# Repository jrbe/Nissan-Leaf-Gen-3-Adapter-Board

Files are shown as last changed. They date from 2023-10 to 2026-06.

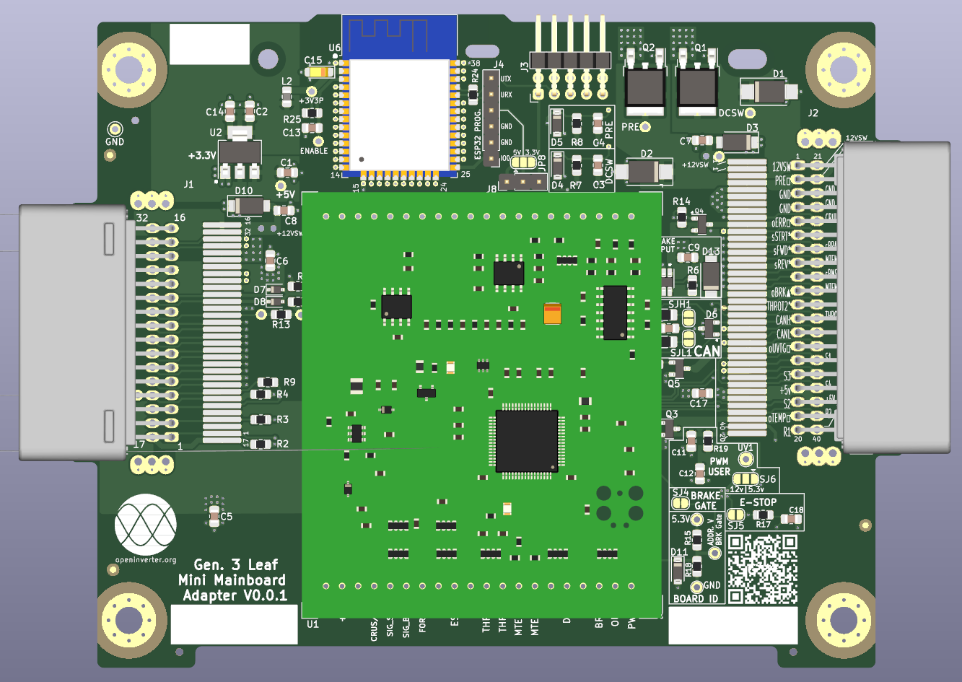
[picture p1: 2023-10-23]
Front PCB Assembly.PNG

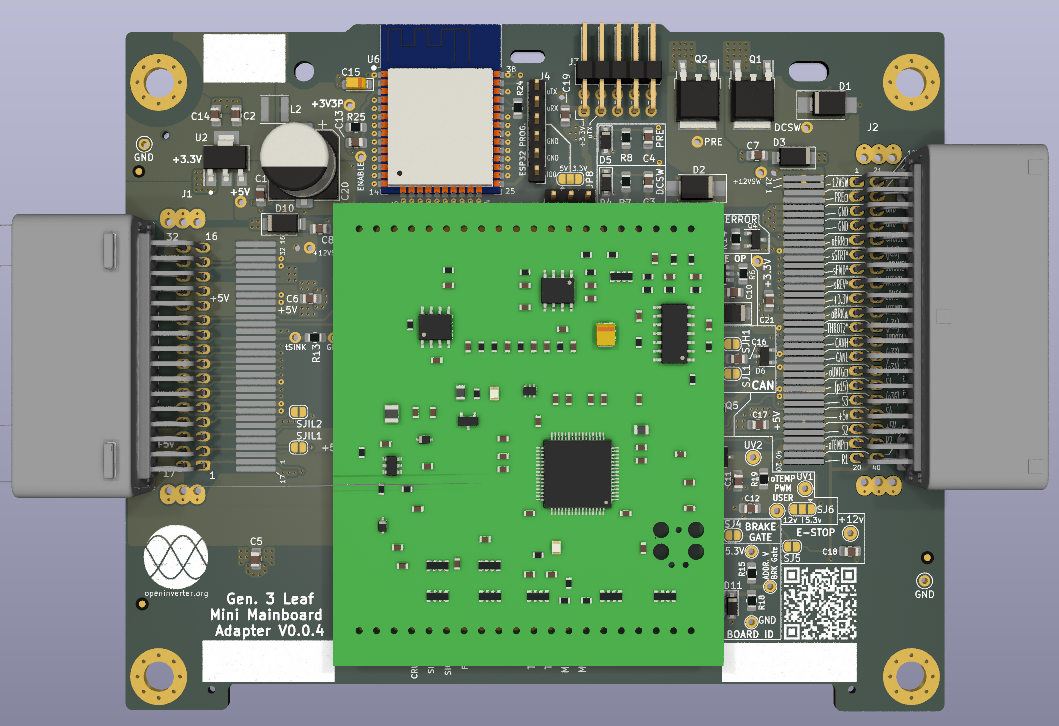
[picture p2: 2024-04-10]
V0.0.4/PC Board Images/All.PNG

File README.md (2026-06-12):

# Nissan-Leaf-Gen-3-Adapter-Board
This is an Open Inverter Mini Mainboard adapter PC board for a Gen. 3 Nissan Leaf inverter. This gives a user full control over the inverter for DIY EV projects. Designed in Kicad 7.

This is a work in progress, V0.0.4 is current but is not a production release yet.  Johu (Open Inverter) could not get a motor spinning in closed loop control. There are also many board settings to work out still.

The Wiki for this board is here, https://openinverter.org/wiki/Nissan_Leaf_Gen_3_(2018_up_EM57)

There are many options built into this board. Multi-footprints for the 2 main connectors for SMD and through hole options, E-stop bypass or use, auxiliary outputs with different voltages, etc. See the wiki above for details.

If you have questions please check the Wiki first.  If your question is not answered there please post questions, comments, ideas, etc. in this thread, [https://openinverter.org/forum/viewtopic.php?t=4565](https://openinverter.org/forum/viewtopic.php?t=4565)

Front PCB w- SMD

PCB back

The original development thread is here, https://openinverter.org/forum/viewtopic.php?t=2324  Please do not post questions here.

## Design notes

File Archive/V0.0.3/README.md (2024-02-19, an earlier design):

# Nissan-Leaf-Gen-3-Adapter-Board
Open Inverter Mini Mainboard adapter PC board for a Gen. 3 Nissan Leaf inverter. Designed in Kicad 6.

**Currently working on V0.0.4, I'd suggest waiting for this new version as a few errors will prevent this from working properly.**

This is a work in progress to control the Gen 3 Nissan Leaf inverter with an Open Inverter Mini Mainboard.  There are a few unknowns still at the time of writing this that are all covered in the Wiki.

The Wiki for this board is here, https://openinverter.org/wiki/Nissan_Leaf_Gen_3_(2018_up_EM57)

The original development thread is here, https://openinverter.org/forum/viewtopic.php?t=2324  Please do not post questions here.

If you have questions please check the Wiki first.  If your question is not answered there please post questions, comments, ideas, etc. in this thread, https://openinverter.org/forum/viewtopic.php?t=4276

Front PCB Assembly

Front PCB w- SMD

PCB back

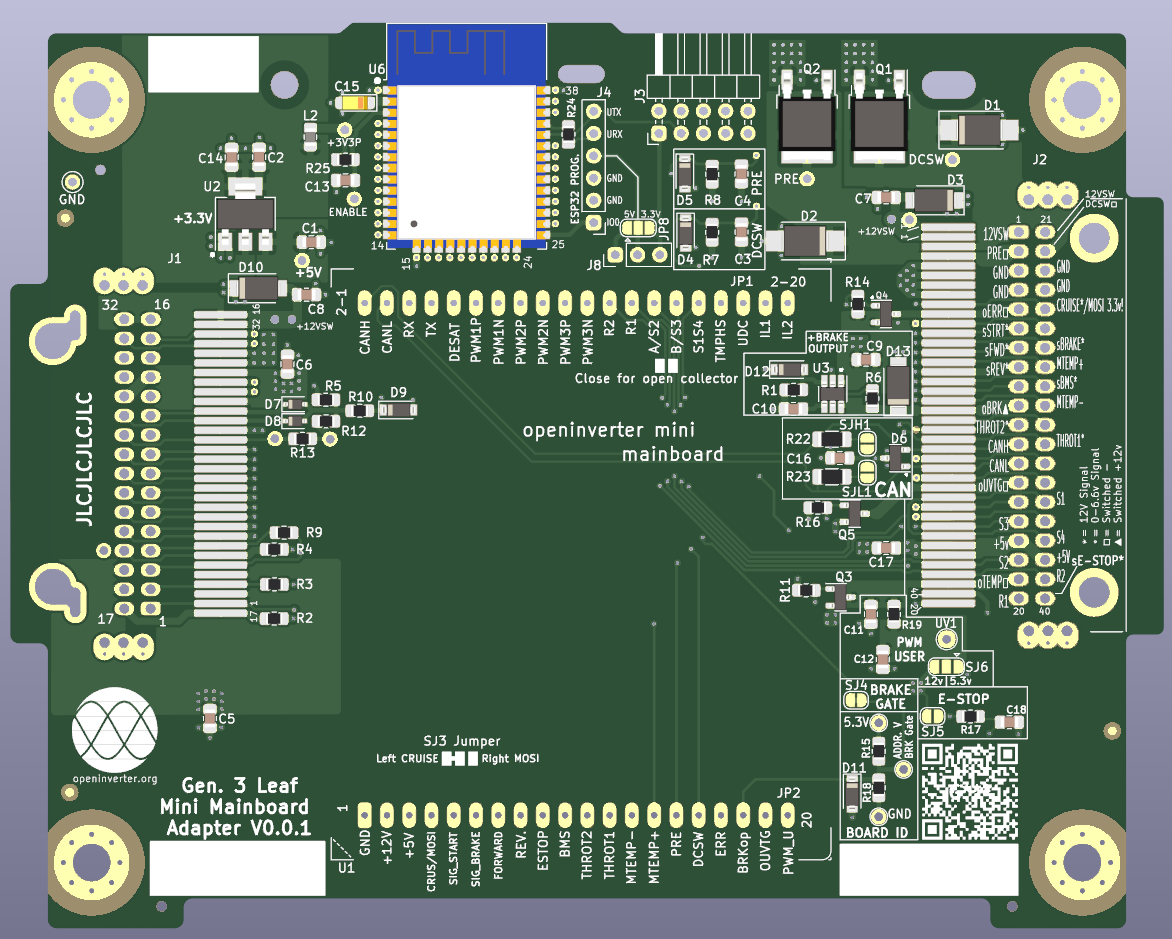
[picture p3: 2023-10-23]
Front PCB w- SMD.PNG

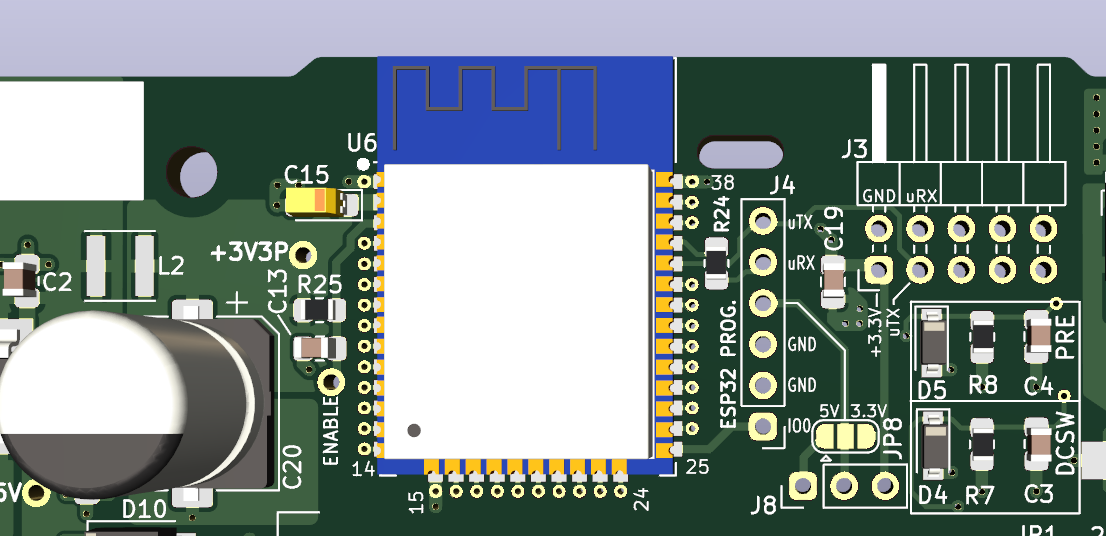
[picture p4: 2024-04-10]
V0.0.4/PC Board Images/ESP32.PNG

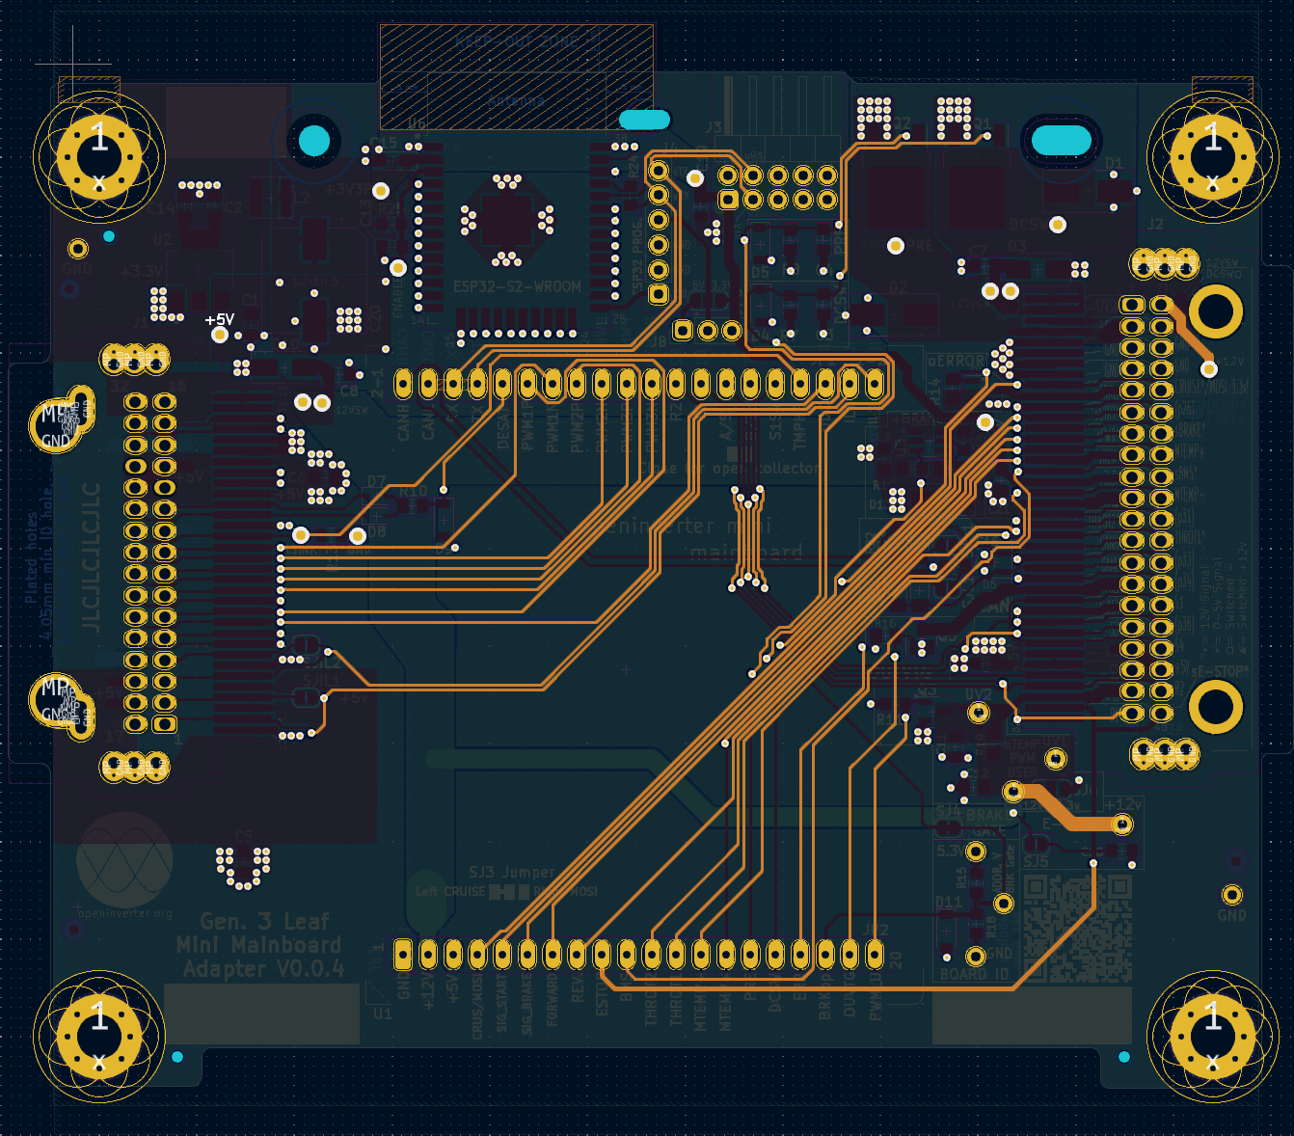
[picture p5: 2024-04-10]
V0.0.4/PC Board Images/3rd Layer, In3Sig.PNG

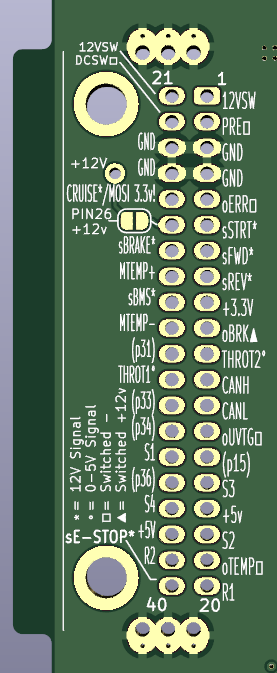
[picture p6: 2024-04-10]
V0.0.4/PC Board Images/40 pos. conn back.PNG

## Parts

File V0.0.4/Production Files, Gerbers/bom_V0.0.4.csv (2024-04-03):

Designator | Footprint | Quantity | Value | LCSC Part #
5.3V1, TP12, TP_A1, TP_GND1_2, TP_GND1, TP_GND2, UV1, UV2, UV3 | TestPoint_THTPad_D2.0mm_Drill1.0mm | 9 | TestPoint | -
C1, C12, C14, C18, C2, C9 | 0805 | 6 | 1uF | C28323
C11, C13, C7, C8 | 0805 | 4 | 100nF | C28233
C15 | CP_EIA-3216-18_Kemet-A_Pad1.58x1.35mm_HandSolder | 1 | 10uF T | C7171
C16 | 0805 | 1 | 4.7nF | C1744
C17, C21, C5, C6 | 0805 | 4 | 10uF | C15850
D1, D2 | D_SMB_Handsoldering | 2 | D_Zener | C1972924
D10, D13, D3 | D_SMA | 3 | SMAJ15CA-TP | C129543
D11, D4, D5, D9 | D_SOD-123 | 4 | MM1Z3B3 | C108453
D6 | SOT-23 | 1 | SP0502BAHT | C907838
D7, D8 | D_SOD-323 | 2 | 1N5819WS Schottky | C191023
H1, H2, H3, H4 | MountingHole_4.3mm_M4_Pad_Via | 4 | MountingHole_Pad | -
H5, H6 | MountingHole_4.3mm_M4 | 2 | MountingHole | -
J4 | PinHeader_1x06_P2.54mm_Vertical | 1 | Conn_01x06_Male | DNP
J8 | PinHeader_1x03_P2.54mm_Vertical | 1 | Conn_01x03_Male | DNP
JP8, SJ6 | SolderJumper-3_P1.3mm_Open_RoundedPad1.0x1.5mm | 2 | Jumper_3_Open | -
L2 | Inductor_Sunlord_4030 | 1 | 10uH | C38117
Q1, Q2 | TO-252-2 | 2 | Q_NMOS_GDS | C3017
Q3, Q4, Q5 | SOT-23 | 3 | IRLML0100TRPBF | C53658
R10 | 0805 | 1 | 470R | C17710
R11, R14, R16, R7, R8 | 0805 | 5 | 10K | C17414
R13 | 0805 | 1 | 1k2 | C17379
R15 | 0805 | 1 | 47K 1pct. | C17713
R18, R25 | 0805 | 2 | 4K7 1pct. | C17673
R22, R23, R32, R33 | 1206 | 4 | 120R .5pct 0.125W+ | C2984524
R24 | 0805 | 1 | 499R | C17722
SJ4 | SolderJumper-2_P1.3mm_Bridged_RoundedPad1.0x1.5mm | 1 | SolderJumper_2_Bridged | -
SJ5 | SolderJumper-2_P1.3mm_Open_RoundedPad1.0x1.5mm | 1 | SolderJumper_2_Bridged | -
SJ9, SJH1, SJIL1, SJIL2, SJL1 | SolderJumper-2_P1.3mm_Open_RoundedPad1.0x1.5mm | 5 | SolderJumper_2_Open | -
U1 | OPENINVERTER_MINI_MAINBOARD | 1 | OpenInverter_Mini_Mainboard-openinverter_mini_mainboard | -
U2 | SOT-223-3_TabPin2 | 1 | AP1117-33 | C6186
U3 | SOT-23-6_Handsoldering | 1 | TPS22810DBVR | C205990
U6 | ESP32-WROOM-32 | 1 | ESP32-S2-WROOM | C82899

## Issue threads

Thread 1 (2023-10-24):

E-Stop / R17 value too high

jrbe, 2023-10-24:
R17 needs to be a very low value to work with the 4k7 / 1k2 voltage divider on the mini mainboard.  As it is in V0.0.1 the e-stop signal will never be seen as high.

jrbe, 2023-10-24:
Removed R17.  Upreved to V0.0.2.

Closed 2023-10-24.

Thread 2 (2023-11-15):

L2 inductor too small

jrbe, 2023-11-15:
The L2 inductor is only rated for 15ma.

jrbe, 2023-11-15:
Changed to a Sunlord 4030 AKA 4x4mm inductor footprint & upreved to V0.0.3.

Closed 2023-11-15.

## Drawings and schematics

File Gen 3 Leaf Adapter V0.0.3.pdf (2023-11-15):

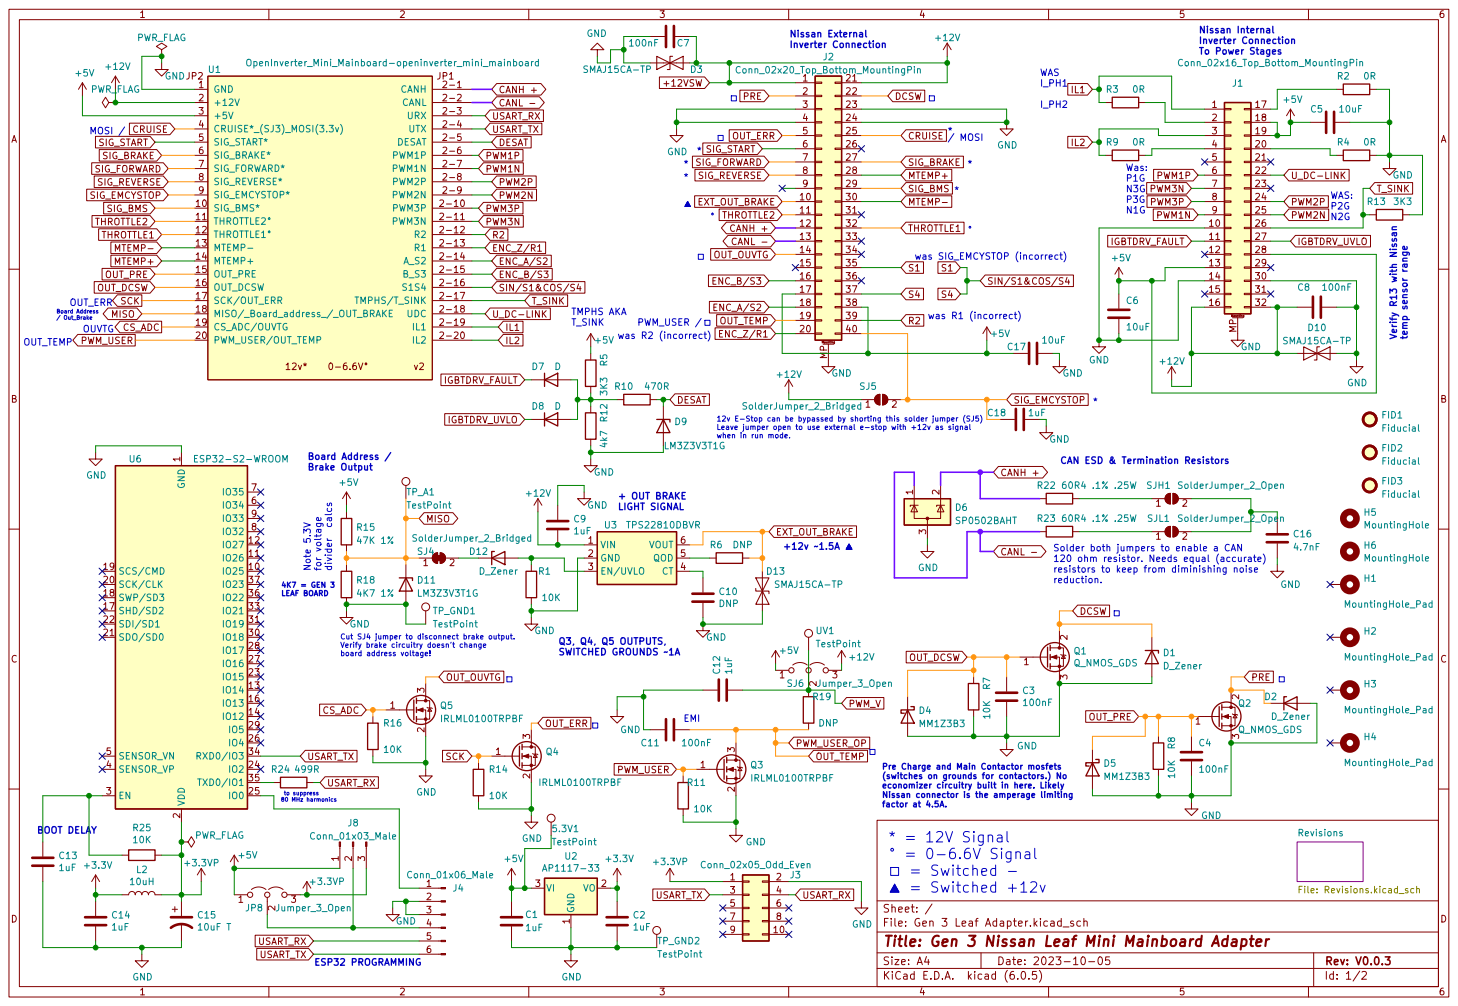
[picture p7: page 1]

To Power Stages + OUT BRAKE
I_PH2 Solder both jumpers to enable a CAN

SCK
PWM_V MISO
resistors to keep from diminishing noise reduction. OUVTG
PWM_USER

120 ohm resistor. Needs equal (accurate)

2 SCK/CLK 20 SDO/SD0 21 SDI/SD1 22

factor at 4.5A. þÿ%¡
Pre Charge and Main Contactor mosfets
(switches on grounds for contactors.) No
economizer circuitry built in here. Likely Nissan connector is the amperage limiting

Id: 1/2 Title: Gen 3 Nissan Leaf Mini Mainboard Adapter

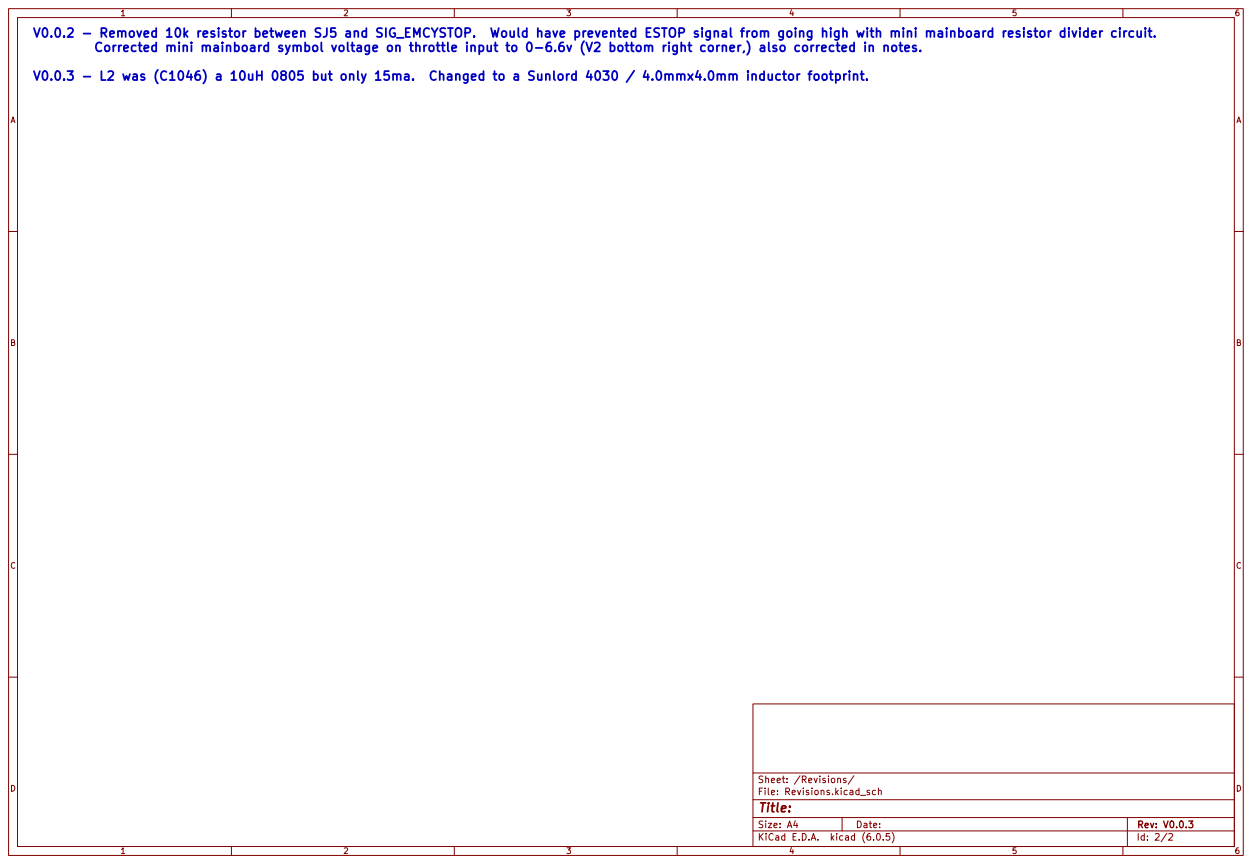
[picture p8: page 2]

V0.0.2 - Removed 10k resistor between SJ5 and SIG_EMCYSTOP. Would have prevented ESTOP signal from going high with mini mainboard resistor divider circuit.
Corrected mini mainboard symbol voltage on throttle input to 0-6.6v (V2 bottom right corner,) also corrected in notes.

V0.0.3 - L2 was (C1046) a 10uH 0805 but only 15ma. Changed to a Sunlord 4030 / 4.0mmx4.0mm inductor footprint.

File: Revisions.kicad_sch Sheet: /Revisions/
Id: 2/2 Title:

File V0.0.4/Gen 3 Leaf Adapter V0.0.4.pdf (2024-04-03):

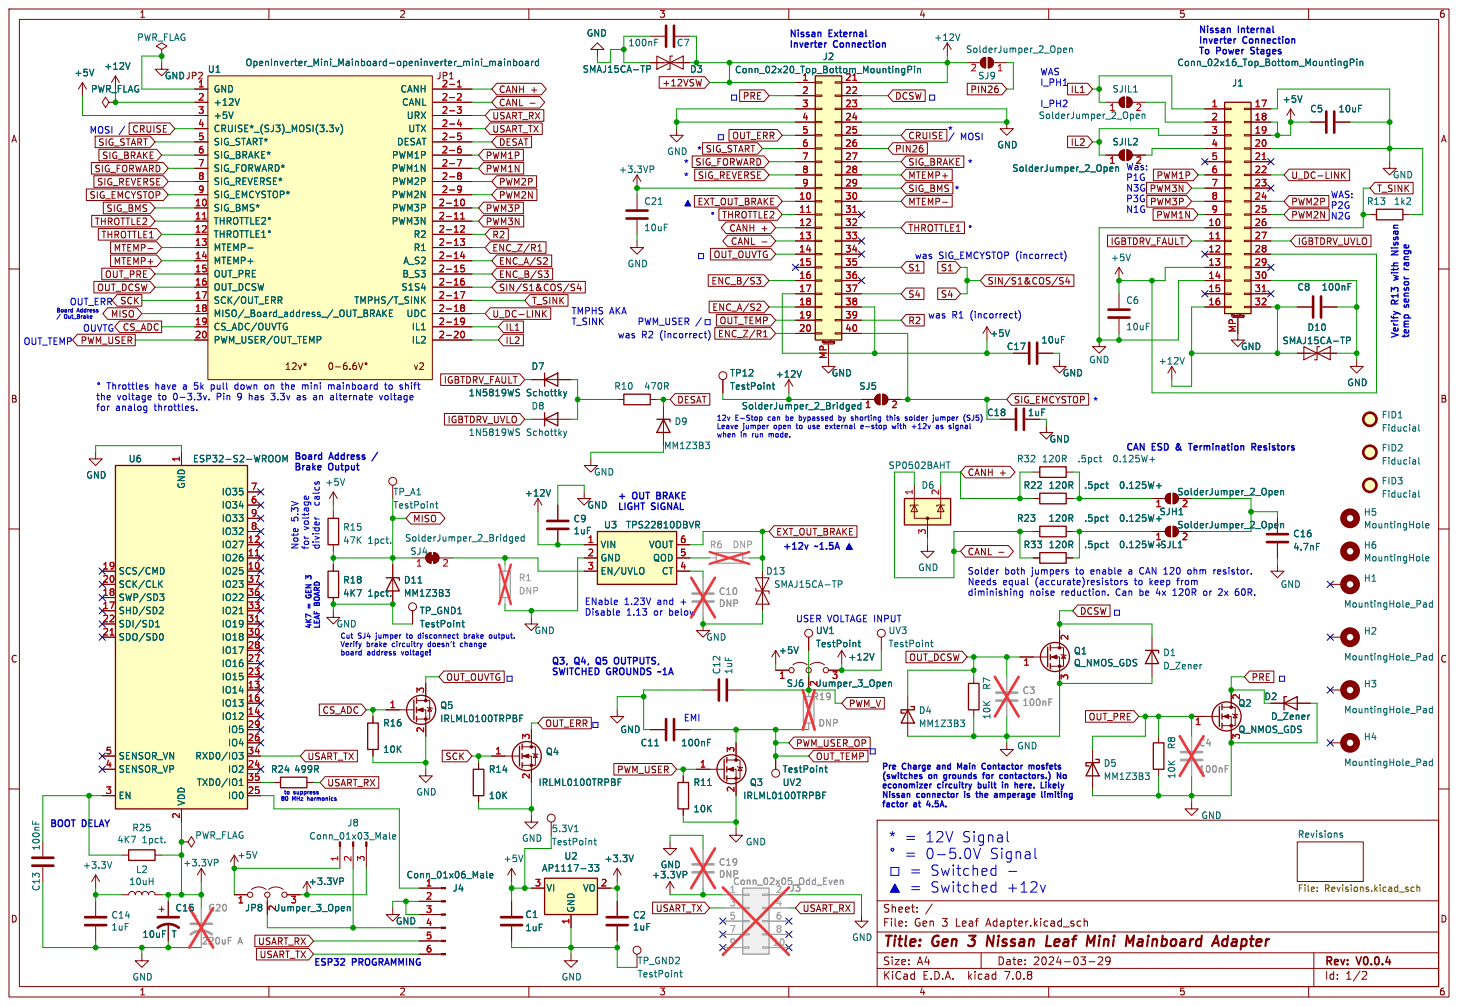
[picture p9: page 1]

GND
To Power Stages Q3, Q4, Q5 OUTPUTS, SWITCHED GROUNDS ~1A

2 SCK/CLK 20 SDO/SD0 21 SDI/SD1 22

Pre Charge and Main Contactor mosfets
factor at 4.5A.
* = 12V Signal
þÿ%¡ = Switched - þÿ%² = Switched +12v

to suppress 80 MHz harmonics

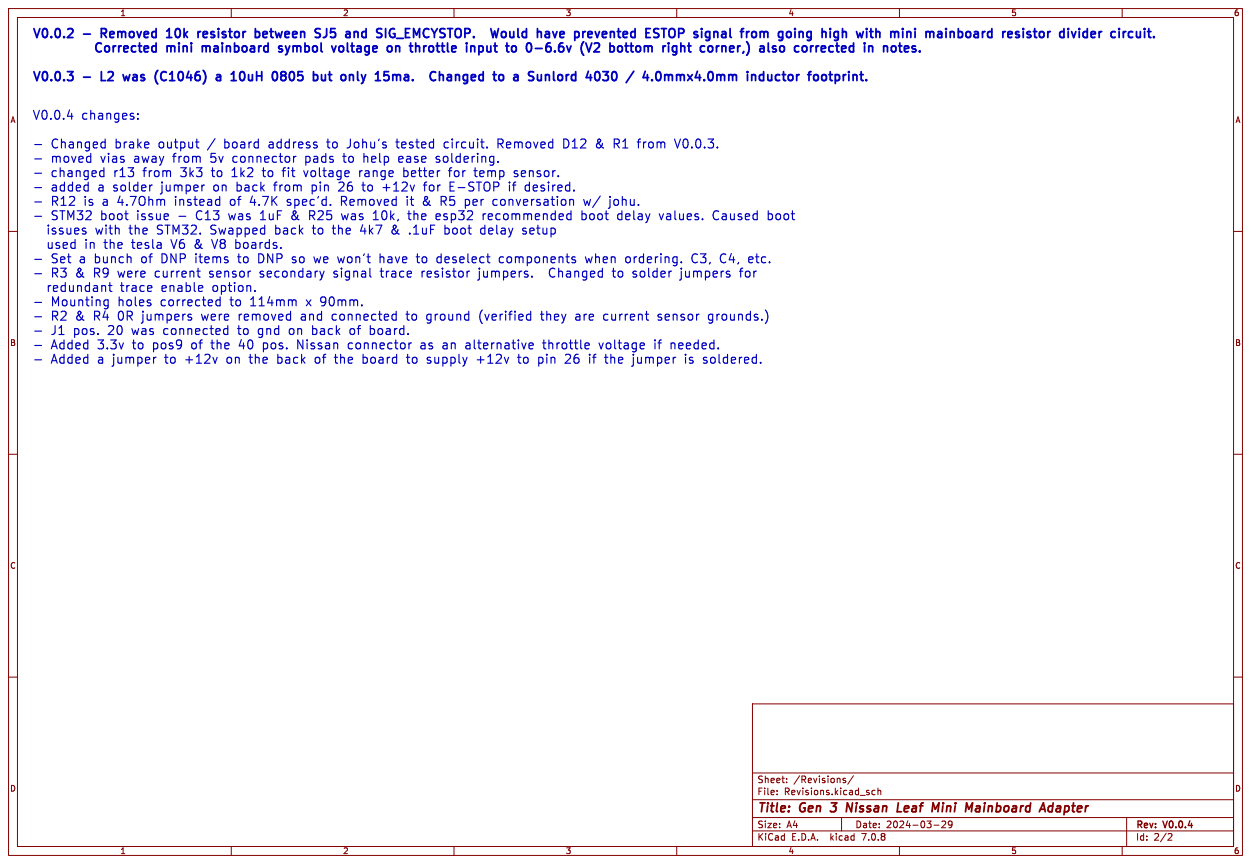
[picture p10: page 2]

issues with the STM32. Swapped back to the 4k7 & .1uF boot delay setup

redundant trace enable option. - Mounting holes corrected to 114mm x 90mm. - R2 & R4 0R jumpers were removed and connected to ground (verified they are current sensor grounds.)

- J1 pos. 20 was connected to gnd on back of board. - Added 3.3v to pos9 of the 40 pos. Nissan connector as an alternative throttle voltage if needed. - Added a jumper to +12v on the back of the board to supply +12v to pin 26 if the jumper is soldered.

Id: 2/2 Title: Gen 3 Nissan Leaf Mini Mainboard Adapter File: Revisions.kicad_sch Sheet: /Revisions/

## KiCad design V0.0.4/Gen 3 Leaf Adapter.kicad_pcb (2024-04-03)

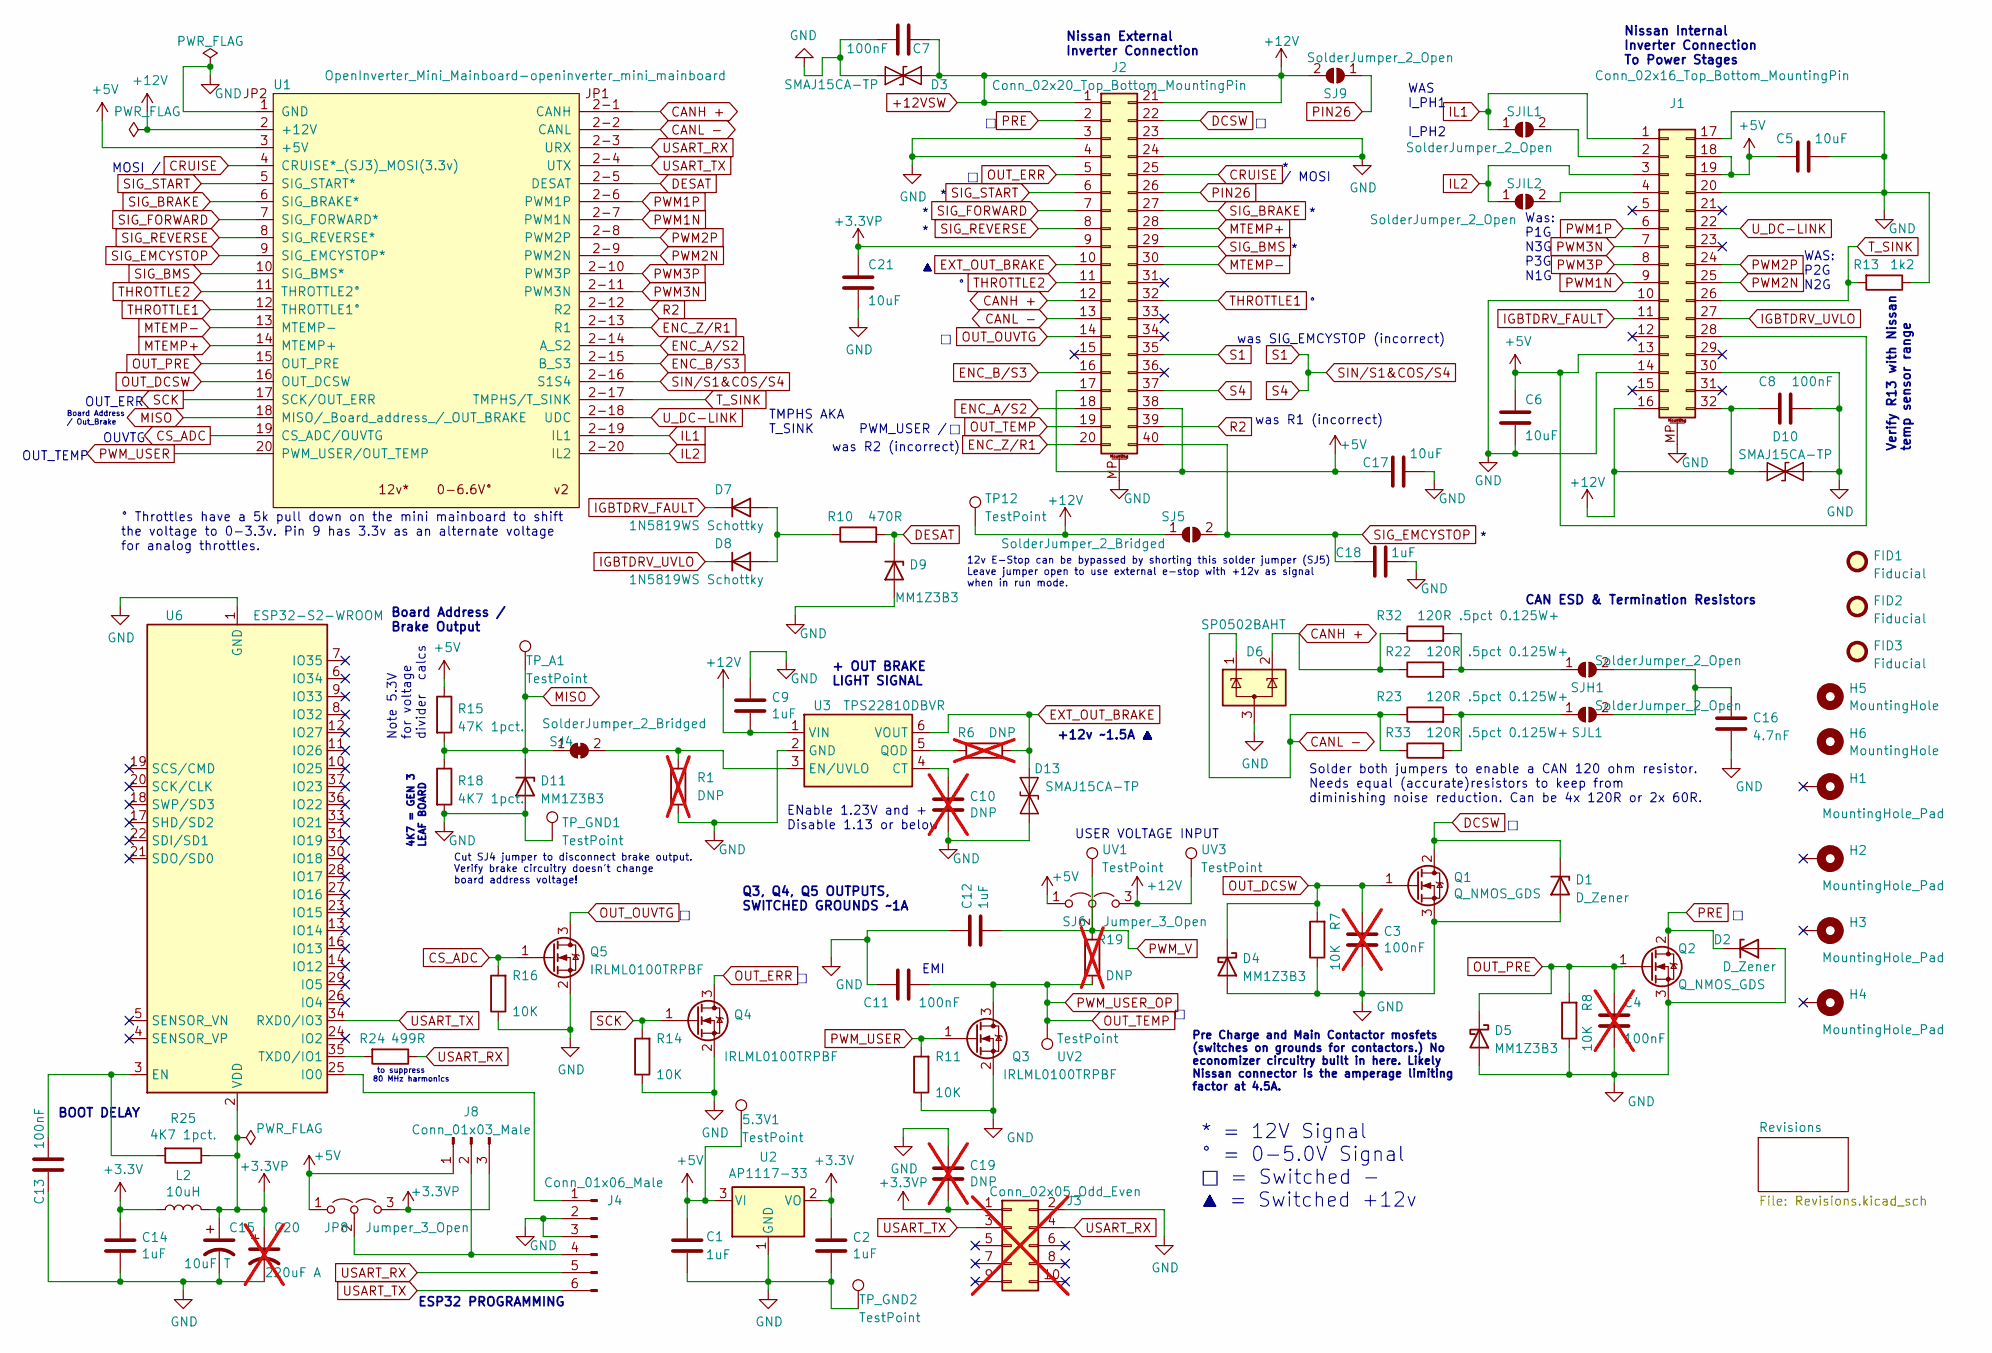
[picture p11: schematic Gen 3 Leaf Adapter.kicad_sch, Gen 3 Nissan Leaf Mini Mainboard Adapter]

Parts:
5.3V1: TestPoint; TestPoint_THTPad_D2.0mm_Drill1.0mm
C1, C2, C9, C12, C14, C18: 1uF; C_0805_2012Metric_Pad1.18x1.45mm_HandSolder; MFG Part # CL21B105KBFNNNE; LCSC Part C28323
C3, C4: 100nF; C_0805_2012Metric_Pad1.18x1.45mm_HandSolder; MFG Part # CL21B104KCFNNNE; LCSC Part C28233; not fitted
C5, C6, C17, C21: 10uF; C_0805_2012Metric_Pad1.18x1.45mm_HandSolder; MFG Part # CL21A106KAYNNNE; LCSC Part C15850
C7, C8, C11, C13: 100nF; C_0805_2012Metric_Pad1.18x1.45mm_HandSolder; MFG Part # CL21B104KCFNNNE; LCSC Part C28233
C10: DNP; C_0805_2012Metric_Pad1.18x1.45mm_HandSolder; LCSC Part DNP; not fitted
C15: 10uF T; CP_EIA-3216-18_Kemet-A_Pad1.58x1.35mm_HandSolder; MFG Part # TAJA106K016RNJ; LCSC Part C7171
C16: 4.7nF; C_0805_2012Metric_Pad1.18x1.45mm_HandSolder; MFG Part # 0805B472K500NT; LCSC Part C1744
C19: DNP; C_0805_2012Metric_Pad1.18x1.45mm_HandSolder; not fitted
C20: 220uF A; CP_Elec_10x10.5; not fitted
D1, D2: D_Zener; D_SMB_Handsoldering; LCSC Part C1972924
D3, D10, D13: SMAJ15CA-TP; D_SMA; MFG Part # SMAJ15CA-TP; LCSC Part C129543
D4, D5, D9, D11: MM1Z3B3; D_SOD-123; MFG Part # MM1Z3B3; LCSC Part C108453
D6: SP0502BAHT; SOT-23; MFG Part # PESD1CAN; LCSC Part C907838
D7, D8: 1N5819WS Schottky; D_SOD-323; MFG Part # 1N5819WS; LCSC Part C191023
FID1, FID2, FID3: Fiducial; Fiducial_1mm_Mask2mm
H1, H2, H3, H4: MountingHole_Pad; MountingHole_4.3mm_M4_Pad_Via
H5, H6: MountingHole; MountingHole_4.3mm_M4
J1: Conn_02x16_Top_Bottom_MountingPin; 32 Pin Internal Nissan Inverter Connector Merged Footprints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; LCSC Part DNP
J2: Conn_02x20_Top_Bottom_MountingPin; TE_1318384-2_Dual_FP; LCSC Part DNP
J3: Conn_02x05_Odd_Even; PinHeader_2x05_P2.54mm_Horizontal; LCSC Part DNP; not fitted
J4: Conn_01x06_Male; PinHeader_1x06_P2.54mm_Vertical; LCSC Part DNP
J8: Conn_01x03_Male; PinHeader_1x03_P2.54mm_Vertical; LCSC Part DNP
JP8: Jumper_3_Open; SolderJumper-3_P1.3mm_Open_RoundedPad1.0x1.5mm
L2: 10uH; Inductor_Sunlord_4030; MFG Part # SWPA4030S100MT; LCSC Part C38117
Q1, Q2: Q_NMOS_GDS; TO-252-2; MFG Part # IRLR3410TRPBF; LCSC Part C3017
Q3, Q4, Q5: IRLML0100TRPBF; SOT-23; MFG Part # IRLML0100TRPBF; LCSC Part C53658
R1: DNP; R_0805_2012Metric_Pad1.20x1.40mm_HandSolder; not fitted
R6, R19: DNP; R_0805_2012Metric_Pad1.20x1.40mm_HandSolder; LCSC Part DNP; not fitted
R7, R8, R11, R14, R16: 10K; R_0805_2012Metric_Pad1.20x1.40mm_HandSolder; MFG Part # 0805W8F1002T5E; LCSC Part C17414
R10: 470R; R_0805_2012Metric_Pad1.20x1.40mm_HandSolder; MFG Part # 0805W8F4700T5E; LCSC Part C17710
R13: 1k2; R_0805_2012Metric_Pad1.20x1.40mm_HandSolder; MFG Part # 0805W8F1201T5E; LCSC Part C17379
R15: 47K 1pct.; R_0805_2012Metric_Pad1.20x1.40mm_HandSolder; MFG Part # 0805W8F4702T5E; LCSC Part C17713
R18, R25: 4K7 1pct.; R_0805_2012Metric_Pad1.20x1.40mm_HandSolder; MFG Part # 0805W8F4701T5E; LCSC Part C17673
R22, R23, R32, R33: 120R .5pct 0.125W+; R_1206_3216Metric_Pad1.30x1.75mm_HandSolder; LCSC Part C2984524
R24: 499R; R_0805_2012Metric_Pad1.20x1.40mm_HandSolder; MFG Part # 0805W8F4990T5E; LCSC Part C17722
SJ4: SolderJumper_2_Bridged; SolderJumper-2_P1.3mm_Bridged_RoundedPad1.0x1.5mm
SJ5: SolderJumper_2_Bridged; SolderJumper-2_P1.3mm_Open_RoundedPad1.0x1.5mm
SJ6: Jumper_3_Open; SolderJumper-3_P1.3mm_Open_RoundedPad1.0x1.5mm
SJ9: SolderJumper_2_Open; SolderJumper-2_P1.3mm_Open_RoundedPad1.0x1.5mm
SJH1: SolderJumper_2_Open; SolderJumper-2_P1.3mm_Open_RoundedPad1.0x1.5mm
SJIL1, SJIL2: SolderJumper_2_Open; SolderJumper-2_P1.3mm_Open_RoundedPad1.0x1.5mm
SJL1: SolderJumper_2_Open; SolderJumper-2_P1.3mm_Open_RoundedPad1.0x1.5mm
TP12: TestPoint; TestPoint_THTPad_D2.0mm_Drill1.0mm
TP_A1: TestPoint; TestPoint_THTPad_D2.0mm_Drill1.0mm
TP_GND1, TP_GND2: TestPoint; TestPoint_THTPad_D2.0mm_Drill1.0mm
U1: OpenInverter_Mini_Mainboard-openinverter_mini_mai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; OPENINVERTER_MINI_MAINBOARD
U2: AP1117-33; SOT-223-3_TabPin2; MFG Part # AMS1117-3.3; LCSC Part C6186
U3: TPS22810DBVR; SOT-23-6_Handsoldering; MFG Part # TPS22810DBVR; LCSC Part C205990
U6: ESP32-S2-WROOM; ESP32-WROOM-32; MFG Part # ESP32-WROOM-32-N4; LCSC Part C82899
UV1, UV2, UV3: TestPoint; TestPoint_THTPad_D2.0mm_Drill1.0mm

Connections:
+3.3VP: C15.1, C19.2, C20.1, C21.1, J2.9, J3.1, J8.3, JP8.3 (B), L2.2, R25.1, U6.2 (VDD)
+3V3: C2.1, C14.1, L2.1, U2.2 (VO)
+5V: 5.3V1.1, C1.1, C5.1, C6.1, C17.1, J1.13, J1.18, J1.19, J1.28, J2.17, J2.38, J8.1, JP8.1 (A), R15.1, SJ6.1 (A), U1.3 (+5V), U2.3 (VI)
+12VSW: C7.1, C8.1, C9.2, D3.2 (A2), D10.2 (A2), J1.16, J1.32, J2.1, J2.21, SJ5.1 (A), SJ6.3 (B), SJ9.2 (B), TP12.1, U1.2 (+12V), U3.1 (VIN), UV3.1
CANH +: D6.2 (K), J2.12, R22.1, R32.1, U1.2-1 (CANH)
CANL -: D6.1 (K), J2.13, R23.1, R33.1, U1.2-2 (CANL)
CRUISE: J2.25, U1.4 (CRUISE*_(SJ3)_MOSI(3.3v))
CS_ADC: Q5.1 (G), R16.2, U1.19 (CS_ADC/OUVTG)
DCSW: D1.1 (K), J2.22, Q1.2 (D)
DESAT: D9.1 (K), R10.2, U1.2-5 (DESAT)
ENC_A/S2: J2.18, U1.2-14 (A_S2)
ENC_B/S3: J2.16, U1.2-15 (B_S3)
ENC_Z/R1: J2.20, U1.2-13 (R1)
EXT_OUT_BRAKE: D13.1 (A1), J2.10, R6.1, U3.6 (VOUT)
GND: C1.2, C2.2, C3.2, C4.2, C5.2, C6.2, C7.2, C8.2, C9.1, C10.2, C11.2, C12.1, C13.1, C14.2, C15.2, C16.2, C17.2, C18.2, C19.1, C20.2, C21.2, D1.2 (A), D2.2 (A), D3.1 (A1), D4.2 (A), D5.2 (A), D6.3 (A), D9.2 (A), D10.1 (A1), D11.2 (A), D13.2 (A2), J1.10, J1.14, J1.17, J1.20, J1.30, J1.MP (MountPin), J2.3, J2.4, J2.23, J2.24, J2.MP (MountPin), J3.2, J4.2, J4.3, Q1.3 (S), Q2.3 (S), Q3.2 (S), Q4.2 (S), Q5.2 (S), R1.2, R7.1, R8.1, R11.1, R13.1, R14.1, R16.1, R18.2, TP_GND1.1, TP_GND2.1, U1.1 (GND), U2.1 (GND), U3.2 (GND), U6.1 (GND), U6.15 (GND), U6.38 (GND), U6.39 (GND); also elsewhere on the board
IGBTDRV_FAULT: D7.1 (K), J1.11
IGBTDRV_UVLO: D8.1 (K), J1.27
IL1: J1.1, SJIL1.1 (A), U1.2-19 (IL1)
IL2: J1.3, SJIL2.1 (A), U1.2-20 (IL2)
MISO: D11.1 (K), R15.2, R18.1, SJ4.1 (A), TP_A1.1, U1.18 (MISO/_Board_address_/_OUT_BRAKE)
MTEMP+: J2.28, U1.14 (MTEMP+)
MTEMP-: J2.30, U1.13 (MTEMP-)
unnamed: D7.2 (A), D8.2 (A), R10.1
unnamed: J1.2, SJIL1.2 (B)
unnamed: J1.4, SJIL2.2 (B)
unnamed: J4.1, U6.25 (IO0)
unnamed: J4.4, J8.2, JP8.2 (C)
unnamed: R1.1, SJ4.2 (B), U3.3 (EN/UVLO)
unnamed: R22.2, R32.2, SJH1.1 (A)
unnamed: C16.1, SJH1.2 (B), SJL1.2 (B)
unnamed: R23.2, R33.2, SJL1.1 (A)
unnamed: C10.1, U3.4 (CT)
unnamed: R6.2, U3.5 (QOD)
unnamed: C13.2, R25.2, U6.3 (EN)
unnamed: R24.2, U6.35 (TXD0/IO1)
OUT_DCSW: C3.1, D4.1 (K), Q1.1 (G), R7.2, U1.16 (OUT_DCSW)
OUT_ERR: J2.5, Q4.3 (D)
OUT_OUVTG: J2.14, Q5.3 (D)
OUT_PRE: C4.1, D5.1 (K), Q2.1 (G), R8.2, U1.15 (OUT_PRE)
OUT_TEMP: C11.1, J2.19, Q3.3 (D), R19.1, UV2.1
PIN26: J2.26, SJ9.1 (A)
PRE: D2.1 (K), J2.2, Q2.2 (D)
PWM1N: J1.9, U1.2-7 (PWM1N)
PWM1P: J1.6, U1.2-6 (PWM1P)
PWM2N: J1.25, U1.2-9 (PWM2N)
PWM2P: J1.24, U1.2-8 (PWM2P)
PWM3N: J1.7, U1.2-11 (PWM3N)
PWM3P: J1.8, U1.2-10 (PWM3P)
PWM_USER: Q3.1 (G), R11.2, U1.20 (PWM_USER/OUT_TEMP)
PWM_V: C12.2, R19.2, SJ6.2 (C), UV1.1
R2: J2.39, U1.2-12 (R2)
S1: J2.35, J2.37, U1.2-16 (S1S4)
SCK: Q4.1 (G), R14.2, U1.17 (SCK/OUT_ERR)
SIG_BMS: J2.29, U1.10 (SIG_BMS*)
SIG_BRAKE: J2.27, U1.6 (SIG_BRAKE*)
SIG_EMCYSTOP: C18.1, J2.40, SJ5.2 (B), U1.9 (SIG_EMCYSTOP*)
SIG_FORWARD: J2.7, U1.7 (SIG_FORWARD*)
SIG_REVERSE: J2.8, U1.8 (SIG_REVERSE*)
SIG_START: J2.6, U1.5 (SIG_START*)
THROTTLE1: J2.32, U1.12 (THROTTLE1°)
THROTTLE2: J2.11, U1.11 (THROTTLE2°)
T_SINK: J1.26, R13.2, U1.2-17 (TMPHS/T_SINK)
USART_RX: J3.4, J4.5, R24.1, U1.2-3 (URX)
USART_TX: J3.3, J4.6, U1.2-4 (UTX), U6.34 (RXD0/IO3)
U_DC-LINK: J1.22, U1.2-18 (UDC)

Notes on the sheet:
PWM_USER /
4K7 = GEN 3 LEAF BOARD
OUT_ERR
/ MOSI
+ OUT BRAKE LIGHT SIGNAL
Was: P1G N3G P3G N1G
BOOT DELAY
TMPHS AKA T_SINK
MOSI /
* = 12V Signal ° = 0-5.0V Signal □ = Switched - ▲ = Switched +12v
EMI
Solder both jumpers to enable a CAN 120 ohm resistor. Needs equal (accurate)resistors to keep from diminishing noise reduction. Can be 4x 120R or 2x 60R.
CAN ESD & Termination Resistors
Board Address / Out_Brake
Nissan Internal Inverter Connection To Power Stages
was R2 (incorrect)
ESP32 PROGRAMMING
Board Address / Brake Output
was R1 (incorrect)
WAS I_PH1 I_PH2
+12v ~1.5A ▲
12v E-Stop can be bypassed by shorting this solder jumper (SJ5) Leave jumper open to use external e-stop with +12v as signal when in run mode.
° Throttles have a 5k pull down on the mini mainboard to shift the voltage to 0-3.3v. Pin 9 has 3.3v as an alternate voltage for analog throttles.
Nissan External Inverter Connection
USER VOLTAGE INPUT
Pre Charge and Main Contactor mosfets (switches on grounds for contactors.) No economizer circuitry built in here. Likely Nissan connector is the amperage limiting factor at 4.5A.
Note 5.3V for voltage divider calcs
Verify R13 with Nissan temp sensor range
OUVTG
was SIG_EMCYSTOP (incorrect)
Cut SJ4 jumper to disconnect brake output. Verify brake circuitry doesn't change board address voltage!
WAS: P2G N2G
ENable 1.23V and + Disable 1.13 or below
to suppress 80 MHz harmonics
OUT_TEMP
Q3, Q4, Q5 OUTPUTS, SWITCHED GROUNDS ~1A

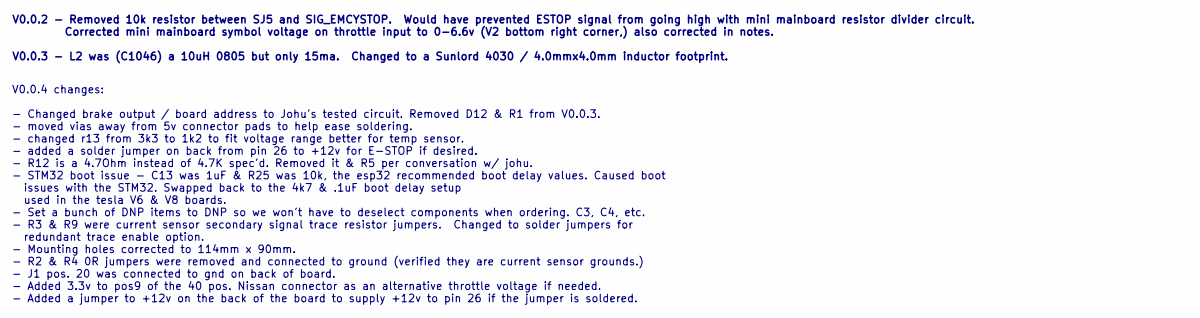
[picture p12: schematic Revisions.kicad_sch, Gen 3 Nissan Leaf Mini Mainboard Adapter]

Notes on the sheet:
V0.0.2 - Removed 10k resistor between SJ5 and SIG_EMCYSTOP. Would have prevented ESTOP signal from going high with mini mainboard resistor divider circuit. Corrected mini mainboard symbol voltage on throttle input to 0-6.6v (V2 bottom right corner,) also corrected in notes. V0.0.3 - L2 was (C1046) 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
V0.0.4 changes: - Changed brake output / board address to Johu's tested circuit. Removed D12 & R1 from V0.0.3. - moved vias away from 5v connector pads to help ease soldering. - changed r13 from 3k3 to 1k2 to fit voltage range better for temp sensor. - added a solder jumper on back from pin 26 to +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

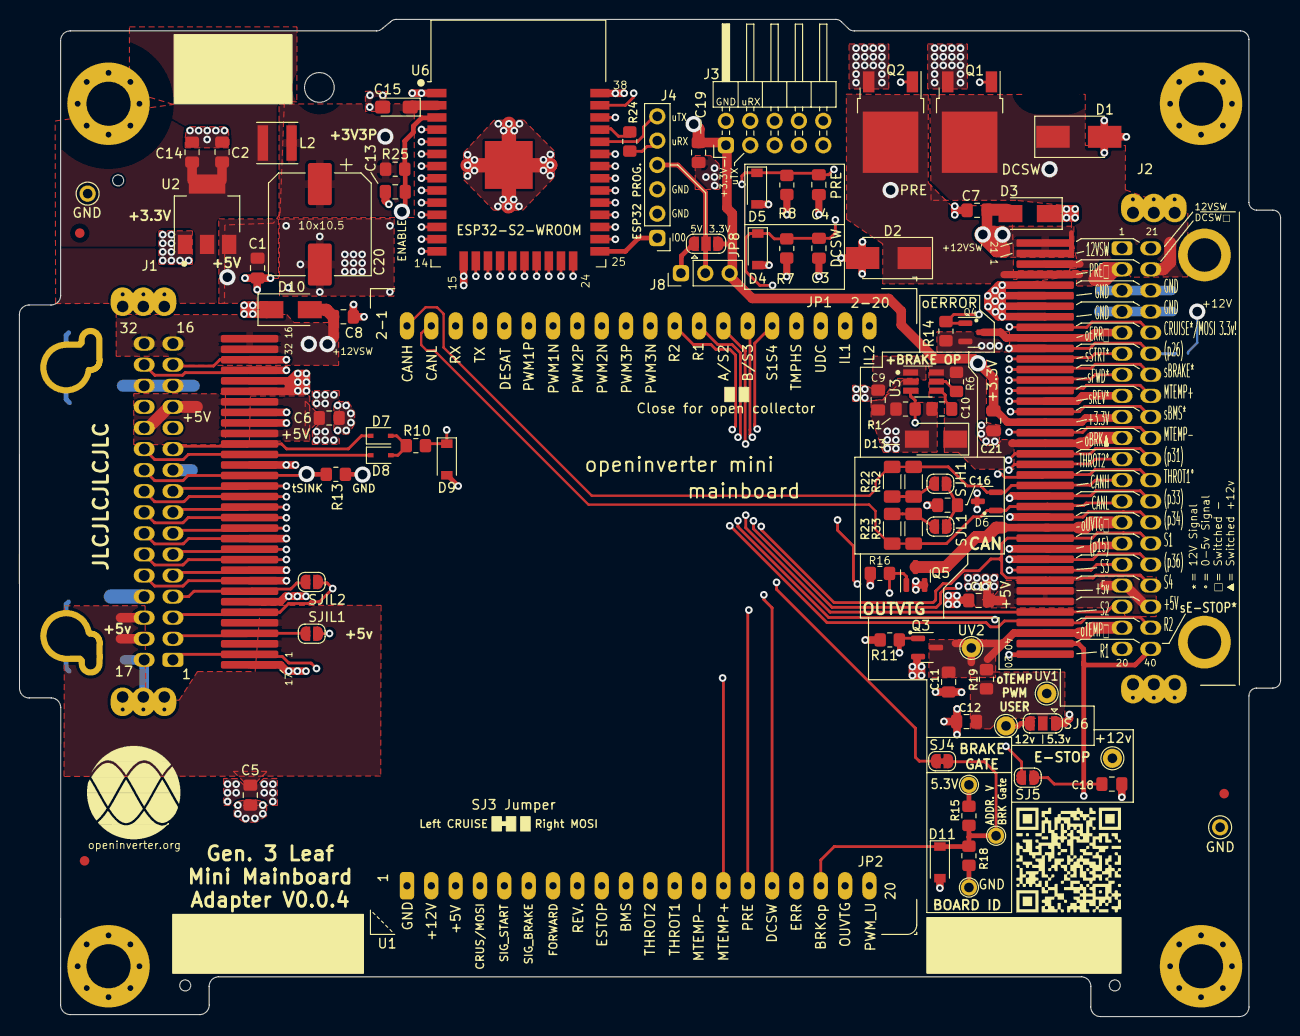
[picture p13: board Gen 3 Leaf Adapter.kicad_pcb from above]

Board: 4 copper layers, 131.6 x 104.0 mm, 94 parts (1 on the bottom side), 65 nets.

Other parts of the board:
TP_GND1#2: TestPoint; TestPoint_THTPad_D2.0mm_Drill1.0mm
U$2: OI_LOGO

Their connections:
GND: TP_GND1#2.1; also elsewhere on the board

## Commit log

2023-10-23 Upload of V0.0.1
    Uploaded the adapter board pcb files done in Kicad 6. This is for 3rd gen (aka gen 3) Nissan Leaf inverters to adapt to using the Open Inverter Mini Mainboard.
    [Gen 3 Leaf Adapter.kicad_pcb, Gen 3 Leaf Adapter.kicad_sch, bom.csv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]
2023-10-24 V0.0.2
    Removed R17, corrected throttle voltages from 0-3.3 to 0-6.6v, corrected schematic notes, mini mainboard symbol (V2), updated silkscreen to V0.0.2, and added a 2nd page to the schematic to track revision changes.
    [Gen 3 Leaf Adapter.kicad_pcb, Gen 3 Leaf Adapter.kicad_sch, Revisions.kicad_sch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]
2023-11-15 V0.0.3 update
    Corrected L2 inductor to one properly sized. From 0805 to a Sunlord 4030 / 4.0mmX4.0mm inductor.
    [Gen 3 Leaf Adapter.kicad_pcb, Gen 3 Leaf Adapter.kicad_sch, Revisions.kicad_sch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]
2023-11-15 V0.0.3 update
    Corrected L2 to a sunlord 4030 / 4x4mm inductor.
    [bom.csv, designators.csv, positions.csv]
2024-04-03 V0.0.4 Upload
    Uploaded V0.0.4. Archived V0.0.3.
    [Gen 3 Leaf Adapter.kicad_pcb, Gen 3 Leaf Adapter.kicad_sch, Revisions.kicad_sch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]
2024-04-10 Added board images
    Added board & layer images
2024-04-11 Added missing Kicad files, tried to correct folder structure to match errors.
    Added missing Kicad files, tried to correct folder structure to match errors.
